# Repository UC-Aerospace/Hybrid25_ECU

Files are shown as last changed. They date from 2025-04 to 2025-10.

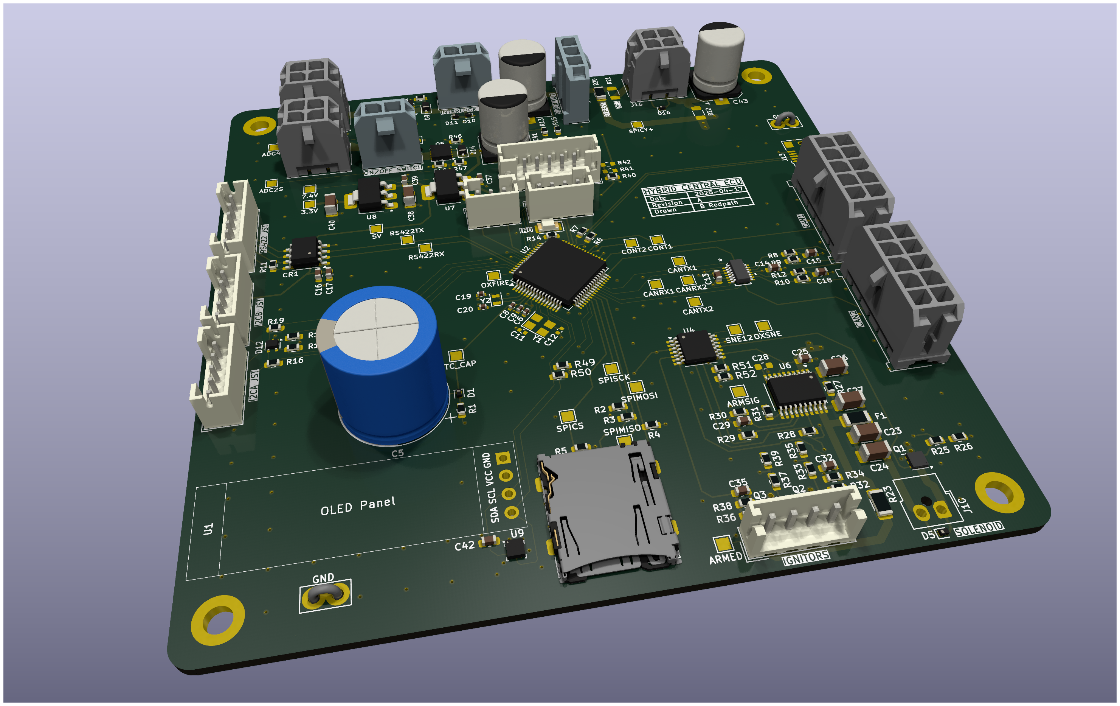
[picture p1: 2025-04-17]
Boards/Central_ECU/Render.png

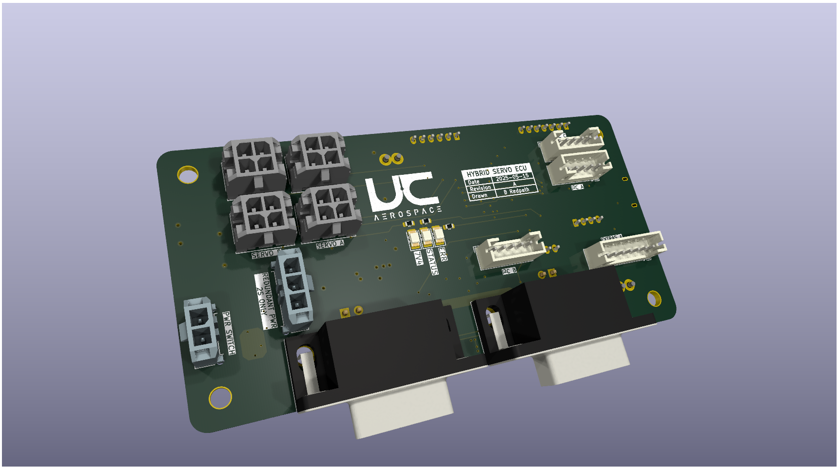
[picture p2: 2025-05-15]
Boards/Servo_Board/Render.png

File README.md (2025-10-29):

# Hybrid Engine Control Unit

This repo contains the hardware and firmware for the 2025 Hybrid Rocket Engine FYP test stand electronics.

The hardware consists of three seperate modules, the central ECU alongside a servo and ADC peripheral. Central to peripheral
communication uses CAN-FD and is designed to be modular, while communications to a remote interface unit is done over RS422.
For more information on the RIU it can be found [here](https://github.com/UC-Aerospace/Hybrid25_RIU).







Hotfire

## Hardware

First thing to note, make sure you read the [issue!](https://github.com/UC-Aerospace/Hybrid25_ECU/issues/1).

There are issues with these designs, keep them in mind for any future development.

### MCU

The hardware of all these boards has been based on the STM32G0 MCU as a platform. The selection process for this was pretty
much based on wanting to use a STM32 for experience and the G0 in particular has two CAN-FD modems and was quite affordable.
This was a mistake, although it ended up working out okay. The STM32G0 critically lacks a SDIO peripheral which is a much
faster and more robust way of interacting with a SD card than SPI, as well as lacking QSPI and only having one SPI bus,
which meant we couldn't implement external flash memory for logging to. Given the issues with SD cards on an actual launch
vechicle that has been experienced I would have the following reccomendations:

* If you make new hardware switch MCU. Still use a ST product but pivot to something with SDIO and QSPI. Look into the F4, F7, H4 and H7 lines.
* Then implement a system where logging happens to flash during a test/launch, and then copies to SD afterwards. This means transfer to a PC
is still easy, you still get the bulk storage of SD but don't rely on it during high vibration periods.
* Don't go for a dual core. The cost increase dosn't justify the advantage and the complexity is significant.
* On cost the total sum of all the electronics this year was large enough not to worry about penny pinching on the MCU you buy maybe 5 of. $8 to $15
is inconsequential and well worth it if it saves you time.

Otherwise though the G0 has served it's purpose well this year. Honestly I have no idea how close we are cutting it with processing time overhead,
the MCU is plenty fast but a lot of the external I/O is quite slow (comms, sensors, SD card). Buffering is the name of the game in cases like that,
and trying to pass as much off to hardware peripherals as possible. Future teams could investigate a switch back to FreeRTOS for more flexibility around
scheduling, this will save some headaches and add a bunch more.

### Layout

Theres a bit of an explaination for the actual hardware design ethos to get you started in the Central ECU board directory. Otherwise between the
boards the main thing to talk about is connectors, comms and power.

The connectors we used on the peripheral boards were a compromise. JST's should never really be used where they might see forces on the wires,
but they are also cheap and the budget was getting out of hand. We mitigated this when testing by externally strain relieving all wires connecting
to both peripheral boards. Also when thinking about connectors try to keep in mind that if something can be plugged into the wrong place, it will
be plugged into the wrong place. Try to keep connectors dissimilar where you can, at least where damage would occur if they went the other way.

Comms is over CAN-FD for the peripheral to central communication and RS422 for central to RIU communication. The descision for this came because
CAN sounded cool to play with and RS422 seemed like the easiest way to get comms upto a couple hundred meters away. Both of these descisions played
out pretty well, with software headaches for both but nothing too serious. The CAN just uses premade serial DB9 cables, as these are cheap and easy
to get hold of. DB9 connectors are really solid and lock well, plus are rated to about 3A per pin. For the link to the RIU we just used generic CAT5
cable, two of the pairs are used for RS422 with another used for the ESTOP signal lines. The plastic connectors on either end are a weakspot, it would
have been nice to use something like etherCON connectors but again, expensive.

Power is something that got changed up a few times. We use lipo batteries as the power source, the ECU has two and theres an extra for the servos. The
ECU has a 2S for general functions, which is also passed to the peripherals which they use. The servo board uses this for the 2 7.4V servos remaining also.
The other battery in the ECU, the 6S, is used for the solenoids and ignitors. This is the power that the ESTOP is inline with, cutting that will abort the
test due to the normally closed solenoid. Finally as we had to add 24V servos there is a seperate 6S battery dedicated to them during the test. This is suboptimal
as we have no insight into the level of it remotely during a test and the standby draw is quite high. If done again just plug this directly into the servo board
and move all servos to 24V. 

## Software

I have yet to find a way to make code sound interesting, and I don't think I'm going to manage it here either. I guess the main thing to point out is there is
a lot of code. Certainly more than I expected going into this, and it took significantly longer than I expected as well. Main word of advice with the software,
it is very easy to get yourself stuck in a trap of rushing rubbish code out.



There was an extended period this year when we were perpetually two weeks away from testing, and it probably shows in the code. In the end the hold up was with
another system, but the code was still blasted out dangerously fast regardless. Give yourself time in the beginning and temper the goals, its easy to add more
later but hard to strip them away with testing looming.

For some more specifics on the actual code I'll leave a quick README for the specifics under each boards code. Heres a quick rant from the EOY report though.

*All code and hardware design has been done in a single git repository. This was poor practice, in future break the code up into separate repositories, 
the only reason we could make a single repository work is because only one person was working on it. One of the main motivators for doing it this way was to enable
code reuse between the boards, for example the CAN module is common between all three and uses a symbolic linked folder. In future it would be worth investigating
using git submodules for the same thing. VS Code was used as the IDE for the ECU and peripherals, while STM32CubeIDE was used for the RIU. It is **strongly** recommended
that future teams do not use CubeIDE, while IDE’s are a preference eclipse is objectively terrible. The ST support for VS Code is good enough now that after installing
the extensions and CubeMX the development experience is much better.*

*The general layout for each board is given below:*



### Finite State Machine Diagrams

#### Central ECU



#### Servo Module



### ADC Module

The ADC module has no inherent state machine, it just reads sensors and sends these.

## Operational

### Safety

Safety has been one of the major concerns with this project. To try and mitigate some of those concerns the main solenoid
is normally closed, such that within 350 milliseconds of cutting the power it fully shuts. The ignitors, being potentially
explosive, were also identified as high risk. Therefore, both these items are on a seperate circuit. Two air gaps exist
in this loop, one E-Stop positioned inline and outside the test container, another at the RIU and connected through a relay
to limit current loss.





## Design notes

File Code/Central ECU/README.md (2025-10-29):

# Central ECU Code

If its your job in 2026 to work on this, good luck. Hopefully the base here is firm enough to build on but the code was
undeniably rushed. To get you started though:

### Layout

* All the user code is in the src/ or include/ folders. Everything else is the STM HAL primarily.
* The Core/Src/main.c file is the main code entry, this has been patched to call src/app.c after it sets everything up.
* The CMakeLists might have to be changed from time to time as well.
* A seriously major battle was fought over getting the SD card working.
Some of the FATFS files were modified in other places, the stuff I added is mainly in Middlewares/Third_Party/FatFs. I really hope no one else has to touch that.

The ECU_Mainboard.ioc can be opened in cubemx to configure most of the HAL options.

### Gotchas

1) The code is currently locked to a specific MCU. This is because I have a habbit of flashing the wrong code when working with
multiple tabs. It checks the UID of the MCU on entry to app.c and will abort if it dosn't match.
2) The code is set up with the intention to support more boards being added modularly but there would be at least a bit of work that has
to go into tweaking the communication protocols I suspect.
3) The SD card is slooooow. It can sometimes take upto 100ms, generally on a flush but it can be hard to predict. This is the reason a lot
of the buffers are so large.
4) The timebase has been changed from a systick interrupt to one of the hardware timers. This still drifts quite quickly (1ms+ every 10 seconds)
compared to the other boards. Switching all from the internal occilator to an external one by populating the part across all boards would improve this.

### Tasks

To see all the tasks head into the app.c file. The timings allocated to these could definitly be optimised but these were pretty much just what worked.
For a quick explaination of each:

#### task_poll_can_handlers()

CAN operates on a two level system. All frames have a priority set by the ID, priority 0 and 1 (error and heartbeat) and serviced in ISR context,
while priorities 2 and 3 (commands and data) are added to a buffer by the ISR and it returns. This buffer is then polled from the can_handler module,
which will decode it and take action based on the contents.

#### task_poll_rs422()

Similarly to how the CAN works the RS422 again uses a hardware and handler approach. This time as the RS422 is really just a UART peripheral the RX fifo
is serviced with DMA into a large circular buffer. This polling function then checks the circular buffer, and after checking the length byte if a full
frame exists in the buffer it will compute a CRC to validate it before decoding and actioning.

#### task_poll_battery()

Pretty simple this one, both batteries are connected to a ADC pin through a voltage divider so a reading is taken, converted to a voltage and then to a
percentage with a lookup table. This updates the OLED screen as well as sending the percentages over RS422.

#### test_servo_poll()

This is the debug USB interface and could be safely disabled for tests. This exposes a command line input over the USB serial port, both for moving the
servos and setting the internal real-time clock that is used in logs.

#### task_flush_sd_card()

When a write happens to the SD card it dosn't really occur. The SD card needs to be flushed to retain this after power loss, so we have to flush it every
now and again. Be warned, flushes can be slooow.

#### fsm_tick()

The main finite state machine, run the next iteration of it.

#### can_service_tx_queue()

Similarly to the revieve this will place messages from the software queue into the hardware tx queue. Upto 3 messages can be in the hardware buffer at once.

#### task_send_heartbeat()

Sends a heartbeat both over CAN broadcast and RS422.

#### spicy_send_status_update()

This is a really dumb name, but "spicy" refers to anything with the ignitors and solenoid which are on the "spicy" circuit. The RS422 frame for this was added
late, hence having its own task. It just sends a bunch of status information.

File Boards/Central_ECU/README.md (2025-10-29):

# Central ECU



The central ECU is pretty simple and carries out a couple of tasks. Firstly is comms which is easy to see with CAN on the left and RS422 on the right
of the schematic. The SD card occupies the top right, with pull up resistors on the main data lines. The top right has a display over I2C and a
pressure and temp sensor. On the status LED front the other boards had two controlled from GPIOs while the central ECU only has one. Two is much
better as you can have a status and error LED, don't discount just how useful a few LEDs are. And finally the interesting bit is probably the spicy stuff.



This is for the control of the single solenoid and two ignitor channels. The layout is very similar for both, except the ignitors have continuity detection
as well. First off theres a connector populated to allow for an external regulator if the voltage requirements of the solenoid changes. This occured as we
made this board before selecting a solenoid. A comparator then is used on the input so we know when the RIU and external ESTOP are released.

For the actual switching there is both a high and low side switch. The high side switch is common to both ignitors and solenoid, and comes in the form of a
EFuse. Theres some big advantages to doing it this way, for one it limits the current spike that occurs when switching the outputs, and also will protect the
circuit in the case of a shorted output. A GPIO toggles this, allowing for a hardware "Arm" controlled by software. A 2K resistor bypasses the highside switch,
this allows for continuity detection. Nominally no current will flow through this as the low side switches will be off, but even if one of the low side switches
is on the current is limited to 15mA, too low to ignite one of the ignitors or open the solenoid. This dual switching design also provides some reassurance in
the case of a FET failing as they usually fail shorted, allowing the test to be terminated by the ECU regardless of a single failure.



The connectors are another area that might be worth mentioning briefly. It is generally good practice to make sure that things physically can't be plugged in
wrong, because someone will definitly plug that 6S battery into your 2S circuit otherwise. You can see I have designed it such that the 2S and 6S input shares
the same sort of connector, but has the voltage on a different pin so if they get plugged in the wrong way around it dosn't matter. Doing this everywhere will
get impractical, for instance the on and arm switches are the same, but think about the critical places to do this and make sure you do. Either use a different
connector type or different number of pins to switch it up.

Final rant for this section, be careful with your linear voltage regulators. They will have a rated current but thats never really achievable due to thermals.
Make sure you actually do some thermal calculations and stitch the regulators through into the planes underneath with plenty of vias. And chaining the regulators
is another approach, I needed 5V but had very little 5V draw, so by inputting 5V to the 3.3V regulator you effectivly split the heat across both regulators.

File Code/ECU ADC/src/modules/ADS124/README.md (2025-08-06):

# ADS124S08 HAL Conversion for STM32

This document describes the conversion of the ADS124S08 Hardware Abstraction Layer (HAL) from TI Drivers to STM32 HAL.

## Overview

The ADS124S08 is a precision, 24-bit analog-to-digital converter (ADC) that communicates via SPI. The original code was designed for TI microcontrollers using TI Drivers. This conversion adapts it for STM32 microcontrollers using the STM32 HAL library.

## Changes Made

### 1. Header Files (`hal.h`)
- Replaced TI Drivers includes with STM32 HAL includes
- Updated pin definitions to match STM32G0 GPIO pins
- Converted function prototypes to use `SPI_HandleTypeDef*` instead of `SPI_Handle`

### 2. Implementation Files (`hal.c`)
- **Timing functions**: 
  - `delay_ms()`: Now uses `HAL_Delay()`
  - `delay_us()`: Implemented using cycle counting for microsecond precision
- **GPIO functions**: 
  - Converted to use `HAL_GPIO_WritePin()` and `HAL_GPIO_ReadPin()`
  - Updated interrupt handling to use STM32 EXTI callbacks
- **SPI functions**: 
  - Converted to use `HAL_SPI_TransmitReceive()`
  - Removed manual CS control (now handled by SPI peripheral)

### 3. ADS124 Driver (`ads124.c` and `ads124.h`)
- Updated all function signatures to use `SPI_HandleTypeDef*`
- Converted all SPI communication calls to use the new HAL functions

## Pin Mapping

The following STM32G0 pins are used for the ADS124S08 interface:

| ADS124S08 Signal | STM32G0 Pin | Description |
|---|---|---|
| nDRDY | PC5 (ADC_RDY) | Data Ready interrupt (falling edge) |
| nRESET | PB0 (ADC_RST) | Reset pin (active low) |
| START/SYNC | PC4 (SYNC) | Start/Sync pin |
| nCS | PA4 (SPI1_NSS)| Chip Select (auto-controlled by SPI) |
| SCLK | PA5 (SPI1_SCK)| SPI Clock |
| DIN | PA7 (SPI1_MOSI)| SPI Master Out Slave In |
| DOUT | PA6 (SPI1_MISO)| SPI Master In Slave Out |

## Usage Example

**IMPORTANT:** The `HAL_GPIO_EXTI_Callback` function MUST be implemented in your `main.c` file, not in the HAL library files. This is because it's a weak function in the STM32 HAL that needs to be overridden in your main application.

```c
#include "ads124_example.h"
#include "hal.h"  // For ads124_gpio_exti_callback

int main(void)
{
    // STM32 HAL initialization (generated by STM32CubeMX)
    HAL_Init();
    SystemClock_Config();
    MX_GPIO_Init();
    MX_SPI1_Init();
    
    // Initialize ADS124S08
    if (ads124_init() != HAL_OK) {
        Error_Handler();
    }
    
    // Start conversions
    ads124_start_conversion();
    
    // Main loop
    while (1) {
        int32_t adc_value;
        uint8_t status;
        
        if (ads124_read_conversion(&adc_value, &status) == HAL_OK) {
            // Process ADC value
            float voltage = (float)adc_value * 2.5f / 8388608.0f;
            // Do something with voltage...
        }
        
        HAL_Delay(100);
    }
}

// CRITICAL: This function MUST be in main.c to handle interrupts properly
void HAL_GPIO_EXTI_Callback(uint16_t GPIO_Pin)
{
    // Call the ADS124 interrupt handler
    ads124_gpio_exti_callback(GPIO_Pin);
    
    // Handle other GPIO interrupts if needed
    // if (GPIO_Pin == OTHER_PIN) { ... }
}
```

## STM32CubeMX Configuration

### SPI1 Configuration
- Mode: Full-Duplex Master
- Hardware NSS Signal: Output
- Clock Polarity: Low (CPOL = 0)
- Clock Phase: 2 Edge (CPHA = 1)
- Data Size: 8 Bits
- Baud Rate: 2 MHz (or as needed)

### GPIO Configuration
- PC5 (ADC_RDY): GPIO_EXTI5, Falling Edge, Pull-up
- PB0 (ADC_RST): GPIO_Output, High level
- PC4 (SYNC): GPIO_Output, Low level

### Interrupt Configuration
- Enable EXTI4_15_IRQn for the DRDY interrupt

## Important Notes

1. **SPI Mode**: The ADS124S08 requires SPI Mode 1 (CPOL=0, CPHA=1)
2. **Timing**: The microsecond delay function uses cycle counting and may need calibration for precise timing
3. **CRITICAL - Interrupts**: The `HAL_GPIO_EXTI_Callback` function MUST be implemented in your main.c file, not in the HAL library. This is because it's a weak function in STM32 HAL that needs to be overridden in the main application.
4. **CS Control**: Chip Select is handled automatically by the SPI peripheral in NSS Output mode
5. **Error Handling**: All SPI operations include error checking and call `Error_Handler()` on failure

### Interrupt Handler Implementation

The correct way to handle the ADS124S08 interrupt is:

1. **In your main.c file**, implement `HAL_GPIO_EXTI_Callback`:
```c
void HAL_GPIO_EXTI_Callback(uint16_t GPIO_Pin)
{
    ads124_gpio_exti_callback(GPIO_Pin);  // Call ADS124 handler
    // Handle other pins if needed
}
```

2. **Include the header**: `#include "hal.h"` in your main.c to access `ads124_gpio_exti_callback`

3. **Do NOT** define `HAL_GPIO_EXTI_Callback` in library files - it won't be called by the linker.

## Files Modified/Created

### Modified Files:
- `src/modules/ADS124/hal.h` - Updated for STM32 HAL
- `src/modules/ADS124/hal.c` - Converted to STM32 HAL implementation
- `src/modules/ADS124/ads124.h` - Updated function prototypes
- `src/modules/ADS124/ads124.c` - Updated function implementations

### New Files:
- `src/modules/ADS124/ads124_example.h` - Example usage header
- `src/modules/ADS124/ads124_example.c` - Example implementation

## Testing

To test the converted HAL:

1. Configure STM32CubeMX as described above
2. Include the ADS124 files in your project
3. Implement the example code in your main application
4. Verify SPI communication and ADC readings

## Future Improvements

1. Implement DWT-based microsecond timing for better precision
2. Add support for manual CS control if needed
3. Add comprehensive error handling and status reporting
4. Implement advanced ADS124S08 features (multiple channels, calibration, etc.)

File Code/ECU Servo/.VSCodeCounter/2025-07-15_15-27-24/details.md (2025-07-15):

# Details

Date : 2025-07-15 15:27:24

Directory /Users/bradr/Uni/FYP/Hybrid25_ECU/Code/ECU Servo

Total : 161 files,  93055 codes, 75724 comments, 24840 blanks, all 193619 lines

[Summary](results.md) / Details / [Diff Summary](diff.md) / [Diff Details](diff-details.md)

## Files
| filename | language | code | comment | blank | total |
| :--- | :--- | ---: | ---: | ---: | ---: |
| [CMakeCache.txt](/CMakeCache.txt) | CMake Cache | 329 | 0 | 73 | 402 |
| [CMakeFiles/4.0.1/CMakeASMCompiler.cmake](/CMakeFiles/4.0.1/CMakeASMCompiler.cmake) | CMake | 24 | 0 | 7 | 31 |
| [CMakeFiles/4.0.1/CMakeCCompiler.cmake](/CMakeFiles/4.0.1/CMakeCCompiler.cmake) | CMake | 66 | 0 | 18 | 84 |
| [CMakeFiles/4.0.1/CMakeCXXCompiler.cmake](/CMakeFiles/4.0.1/CMakeCXXCompiler.cmake) | CMake | 82 | 0 | 26 | 108 |
| [CMakeFiles/4.0.1/CMakeSystem.cmake](/CMakeFiles/4.0.1/CMakeSystem.cmake) | CMake | 10 | 0 | 6 | 16 |
| [CMakeFiles/4.0.1/CompilerIdC/CMakeCCompilerId.c](/CMakeFiles/4.0.1/CompilerIdC/CMakeCCompilerId.c) | C | 690 | 61 | 155 | 906 |
| [CMakeFiles/4.0.1/CompilerIdCXX/CMakeCXXCompilerId.cpp](/CMakeFiles/4.0.1/CompilerIdCXX/CMakeCXXCompilerId.cpp) | C++ | 708 | 62 | 151 | 921 |
| [CMakeFiles/CMakeConfigureLog.yaml](/CMakeFiles/CMakeConfigureLog.yaml) | YAML | 402 | 4 | 36 | 442 |
| [CMakeFiles/InstallScripts.json](/CMakeFiles/InstallScripts.json) | JSON | 8 | 0 | 1 | 9 |
| [CMakeFiles/VerifyGlobs.cmake](/CMakeFiles/VerifyGlobs.cmake) | CMake | 12 | 0 | 2 | 14 |
| [CMakeFiles/clean_additional.cmake](/CMakeFiles/clean_additional.cmake) | CMake | 7 | 0 | 2 | 9 |
| [CMakePresets.json](/CMakePresets.json) | JSON | 60 | 0 | 0 | 60 |
| [Core/Inc/main.h](/Core/Inc/main.h) | C++ | 56 | 39 | 21 | 116 |
| [Core/Inc/stm32g0xx_hal_conf.h](/Core/Inc/stm32g0xx_hal_conf.h) | C++ | 180 | 116 | 56 | 352 |
| [Core/Inc/stm32g0xx_it.h](/Core/Inc/stm32g0xx_it.h) | C++ | 15 | 34 | 15 | 64 |
| [Core/Src/main.c](/Core/Src/main.c) | C | 455 | 237 | 137 | 829 |
| [Core/Src/stm32g0xx_hal_msp.c](/Core/Src/stm32g0xx_hal_msp.c) | C | 279 | 351 | 159 | 789 |
| [Core/Src/stm32g0xx_it.c](/Core/Src/stm32g0xx_it.c) | C | 29 | 96 | 35 | 160 |
| [Core/Src/syscalls.c](/Core/Src/syscalls.c) | C | 123 | 25 | 29 | 177 |
| [Core/Src/sysmem.c](/Core/Src/sysmem.c) | C | 24 | 48 | 8 | 80 |
| [Core/Src/system_stm32g0xx.c](/Core/Src/system_stm32g0xx.c) | C | 74 | 194 | 35 | 303 |
| [Drivers/CMSIS/Device/ST/STM32G0xx/Include/stm32g0b1xx.h](/Drivers/CMSIS/Device/ST/STM32G0xx/Include/stm32g0b1xx.h) | C++ | 9,726 | 829 | 719 | 11,274 |
| [Drivers/CMSIS/Device/ST/STM32G0xx/Include/stm32g0xx.h](/Drivers/CMSIS/Device/ST/STM32G0xx/Include/stm32g0xx.h) | C++ | 119 | 89 | 37 | 245 |
| [Drivers/CMSIS/Device/ST/STM32G0xx/Include/system_stm32g0xx.h](/Drivers/CMSIS/Device/ST/STM32G0xx/Include/system_stm32g0xx.h) | C++ | 14 | 70 | 20 | 104 |
| [Drivers/CMSIS/Include/cmsis_armcc.h](/Drivers/CMSIS/Include/cmsis_armcc.h) | C++ | 401 | 355 | 139 | 895 |
| [Drivers/CMSIS/Include/cmsis_armclang.h](/Drivers/CMSIS/Include/cmsis_armclang.h) | C++ | 623 | 595 | 227 | 1,445 |
| [Drivers/CMSIS/Include/cmsis_armclang_ltm.h](/Drivers/CMSIS/Include/cmsis_armclang_ltm.h) | C++ | 948 | 595 | 349 | 1,892 |
| [Drivers/CMSIS/Include/cmsis_compiler.h](/Drivers/CMSIS/Include/cmsis_compiler.h) | C++ | 207 | 52 | 25 | 284 |
| [Drivers/CMSIS/Include/cmsis_gcc.h](/Drivers/CMSIS/Include/cmsis_gcc.h) | C++ | 1,170 | 620 | 379 | 2,169 |
| [Drivers/CMSIS/Include/cmsis_iccarm.h](/Drivers/CMSIS/Include/cmsis_iccarm.h) | C++ | 769 | 45 | 151 | 965 |
| [Drivers/CMSIS/Include/cmsis_version.h](/Drivers/CMSIS/Include/cmsis_version.h) | C++ | 13 | 23 | 4 | 40 |
| [Drivers/CMSIS/Include/core_armv81mml.h](/Drivers/CMSIS/Include/core_armv81mml.h) | C++ | 1,714 | 651 | 604 | 2,969 |
| [Drivers/CMSIS/Include/core_armv8mbl.h](/Drivers/CMSIS/Include/core_armv8mbl.h) | C++ | 1,033 | 526 | 363 | 1,922 |
| [Drivers/CMSIS/Include/core_armv8mml.h](/Drivers/CMSIS/Include/core_armv8mml.h) | C++ | 1,627 | 642 | 567 | 2,836 |
| [Drivers/CMSIS/Include/core_cm0.h](/Drivers/CMSIS/Include/core_cm0.h) | C++ | 444 | 327 | 182 | 953 |
| [Drivers/CMSIS/Include/core_cm0plus.h](/Drivers/CMSIS/Include/core_cm0plus.h) | C++ | 528 | 346 | 212 | 1,086 |
| [Drivers/CMSIS/Include/core_cm1.h](/Drivers/CMSIS/Include/core_cm1.h) | C++ | 454 | 338 | 188 | 980 |
| [Drivers/CMSIS/Include/core_cm23.h](/Drivers/CMSIS/Include/core_cm23.h) | C++ | 1,081 | 532 | 384 | 1,997 |
| [Drivers/CMSIS/Include/core_cm3.h](/Drivers/CMSIS/Include/core_cm3.h) | C++ | 1,051 | 468 | 419 | 1,938 |
| [Drivers/CMSIS/Include/core_cm33.h](/Drivers/CMSIS/Include/core_cm33.h) | C++ | 1,677 | 646 | 588 | 2,911 |
| [Drivers/CMSIS/Include/core_cm35p.h](/Drivers/CMSIS/Include/core_cm35p.h) | C++ | 1,677 | 646 | 588 | 2,911 |
| [Drivers/CMSIS/Include/core_cm4.h](/Drivers/CMSIS/Include/core_cm4.h) | C++ | 1,182 | 485 | 458 | 2,125 |
| [Drivers/CMSIS/Include/core_cm7.h](/Drivers/CMSIS/Include/core_cm7.h) | C++ | 1,571 | 576 | 579 | 2,726 |
| [Drivers/CMSIS/Include/core_sc000.h](/Drivers/CMSIS/Include/core_sc000.h) | C++ | 488 | 335 | 203 | 1,026 |
| [Drivers/CMSIS/Include/core_sc300.h](/Drivers/CMSIS/Include/core_sc300.h) | C++ | 1,034 | 467 | 412 | 1,913 |
| [Drivers/CMSIS/Include/mpu_armv7.h](/Drivers/CMSIS/Include/mpu_armv7.h) | C++ | 122 | 125 | 26 | 273 |
| [Drivers/CMSIS/Include/mpu_armv8.h](/Drivers/CMSIS/Include/mpu_armv8.h) | C++ | 168 | 135 | 44 | 347 |
| [Drivers/CMSIS/Include/tz_context.h](/Drivers/CMSIS/Include/tz_context.h) | C++ | 19 | 40 | 12 | 71 |
| [Drivers/STM32G0xx_HAL_Driver/Inc/Legacy/stm32_hal_legacy.h](/Drivers/STM32G0xx_HAL_Driver/Inc/Legacy/stm32_hal_legacy.h) | C++ | 2,895 | 616 | 409 | 3,920 |
| [Drivers/STM32G0xx_HAL_Driver/Inc/stm32g0xx_hal.h](/Drivers/STM32G0xx_HAL_Driver/Inc/stm32g0xx_hal.h) | C++ | 460 | 268 | 111 | 839 |
| [Drivers/STM32G0xx_HAL_Driver/Inc/stm32g0xx_hal_adc.h](/Drivers/STM32G0xx_HAL_Driver/Inc/stm32g0xx_hal_adc.h) | C++ | 521 | 1,248 | 175 | 1,944 |
| [Drivers/STM32G0xx_HAL_Driver/Inc/stm32g0xx_hal_adc_ex.h](/Drivers/STM32G0xx_HAL_Driver/Inc/stm32g0xx_hal_adc_ex.h) | C++ | 40 | 111 | 36 | 187 |
| [Drivers/STM32G0xx_HAL_Driver/Inc/stm32g0xx_hal_cortex.h](/Drivers/STM32G0xx_HAL_Driver/Inc/stm32g0xx_hal_cortex.h) | C++ | 164 | 171 | 53 | 388 |
| [Drivers/STM32G0xx_HAL_Driver/Inc/stm32g0xx_hal_def.h](/Drivers/STM32G0xx_HAL_Driver/Inc/stm32g0xx_hal_def.h) | C++ | 108 | 78 | 30 | 216 |
| [Drivers/STM32G0xx_HAL_Driver/Inc/stm32g0xx_hal_dma.h](/Drivers/STM32G0xx_HAL_Driver/Inc/stm32g0xx_hal_dma.h) | C++ | 428 | 274 | 102 | 804 |
| [Drivers/STM32G0xx_HAL_Driver/Inc/stm32g0xx_hal_dma_ex.h](/Drivers/STM32G0xx_HAL_Driver/Inc/stm32g0xx_hal_dma_ex.h) | C++ | 114 | 110 | 55 | 279 |
| [Drivers/STM32G0xx_HAL_Driver/Inc/stm32g0xx_hal_exti.h](/Drivers/STM32G0xx_HAL_Driver/Inc/stm32g0xx_hal_exti.h) | C++ | 201 | 142 | 45 | 388 |
| [Drivers/STM32G0xx_HAL_Driver/Inc/stm32g0xx_hal_fdcan.h](/Drivers/STM32G0xx_HAL_Driver/Inc/stm32g0xx_hal_fdcan.h) | C++ | 622 | 634 | 187 | 1,443 |
| [Drivers/STM32G0xx_HAL_Driver/Inc/stm32g0xx_hal_flash.h](/Drivers/STM32G0xx_HAL_Driver/Inc/stm32g0xx_hal_flash.h) | C++ | 446 | 490 | 98 | 1,034 |
| [Drivers/STM32G0xx_HAL_Driver/Inc/stm32g0xx_hal_flash_ex.h](/Drivers/STM32G0xx_HAL_Driver/Inc/stm32g0xx_hal_flash_ex.h) | C++ | 27 | 72 | 18 | 117 |
| [Drivers/STM32G0xx_HAL_Driver/Inc/stm32g0xx_hal_gpio.h](/Drivers/STM32G0xx_HAL_Driver/Inc/stm32g0xx_hal_gpio.h) | C++ | 124 | 188 | 51 | 363 |
| [Drivers/STM32G0xx_HAL_Driver/Inc/stm32g0xx_hal_gpio_ex.h](/Drivers/STM32G0xx_HAL_Driver/Inc/stm32g0xx_hal_gpio_ex.h) | C++ | 457 | 274 | 106 | 837 |
| [Drivers/STM32G0xx_HAL_Driver/Inc/stm32g0xx_hal_i2c.h](/Drivers/STM32G0xx_HAL_Driver/Inc/stm32g0xx_hal_i2c.h) | C++ | 326 | 396 | 117 | 839 |
| [Drivers/STM32G0xx_HAL_Driver/Inc/stm32g0xx_hal_i2c_ex.h](/Drivers/STM32G0xx_HAL_Driver/Inc/stm32g0xx_hal_i2c_ex.h) | C++ | 45 | 106 | 27 | 178 |
| [Drivers/STM32G0xx_HAL_Driver/Inc/stm32g0xx_hal_pcd.h](/Drivers/STM32G0xx_HAL_Driver/Inc/stm32g0xx_hal_pcd.h) | C++ | 244 | 283 | 103 | 630 |
| [Drivers/STM32G0xx_HAL_Driver/Inc/stm32g0xx_hal_pcd_ex.h](/Drivers/STM32G0xx_HAL_Driver/Inc/stm32g0xx_hal_pcd_ex.h) | C++ | 21 | 47 | 21 | 89 |
| [Drivers/STM32G0xx_HAL_Driver/Inc/stm32g0xx_hal_pwr.h](/Drivers/STM32G0xx_HAL_Driver/Inc/stm32g0xx_hal_pwr.h) | C++ | 100 | 186 | 40 | 326 |
| [Drivers/STM32G0xx_HAL_Driver/Inc/stm32g0xx_hal_pwr_ex.h](/Drivers/STM32G0xx_HAL_Driver/Inc/stm32g0xx_hal_pwr_ex.h) | C++ | 251 | 315 | 76 | 642 |
| [Drivers/STM32G0xx_HAL_Driver/Inc/stm32g0xx_hal_rcc.h](/Drivers/STM32G0xx_HAL_Driver/Inc/stm32g0xx_hal_rcc.h) | C++ | 1,882 | 997 | 291 | 3,170 |
| [Drivers/STM32G0xx_HAL_Driver/Inc/stm32g0xx_hal_rcc_ex.h](/Drivers/STM32G0xx_HAL_Driver/Inc/stm32g0xx_hal_rcc_ex.h) | C++ | 696 | 694 | 201 | 1,591 |
| [Drivers/STM32G0xx_HAL_Driver/Inc/stm32g0xx_hal_rtc.h](/Drivers/STM32G0xx_HAL_Driver/Inc/stm32g0xx_hal_rtc.h) | C++ | 369 | 457 | 164 | 990 |
| [Drivers/STM32G0xx_HAL_Driver/Inc/stm32g0xx_hal_rtc_ex.h](/Drivers/STM32G0xx_HAL_Driver/Inc/stm32g0xx_hal_rtc_ex.h) | C++ | 287 | 705 | 171 | 1,163 |
| [Drivers/STM32G0xx_HAL_Driver/Inc/stm32g0xx_hal_spi.h](/Drivers/STM32G0xx_HAL_Driver/Inc/stm32g0xx_hal_spi.h) | C++ | 298 | 441 | 113 | 852 |
| [Drivers/STM32G0xx_HAL_Driver/Inc/stm32g0xx_hal_spi_ex.h](/Drivers/STM32G0xx_HAL_Driver/Inc/stm32g0xx_hal_spi_ex.h) | C++ | 11 | 49 | 14 | 74 |
| [Drivers/STM32G0xx_HAL_Driver/Inc/stm32g0xx_hal_tim.h](/Drivers/STM32G0xx_HAL_Driver/Inc/stm32g0xx_hal_tim.h) | C++ | 1,136 | 1,064 | 270 | 2,470 |
| [Drivers/STM32G0xx_HAL_Driver/Inc/stm32g0xx_hal_tim_ex.h](/Drivers/STM32G0xx_HAL_Driver/Inc/stm32g0xx_hal_tim_ex.h) | C++ | 231 | 195 | 69 | 495 |
| [Drivers/STM32G0xx_HAL_Driver/Inc/stm32g0xx_hal_uart.h](/Drivers/STM32G0xx_HAL_Driver/Inc/stm32g0xx_hal_uart.h) | C++ | 545 | 997 | 204 | 1,746 |
| [Drivers/STM32G0xx_HAL_Driver/Inc/stm32g0xx_hal_uart_ex.h](/Drivers/STM32G0xx_HAL_Driver/Inc/stm32g0xx_hal_uart_ex.h) | C++ | 543 | 180 | 49 | 772 |
| [Drivers/STM32G0xx_HAL_Driver/Inc/stm32g0xx_ll_adc.h](/Drivers/STM32G0xx_HAL_Driver/Inc/stm32g0xx_ll_adc.h) | C++ | 1,208 | 3,979 | 310 | 5,497 |
| [Drivers/STM32G0xx_HAL_Driver/Inc/stm32g0xx_ll_bus.h](/Drivers/STM32G0xx_HAL_Driver/Inc/stm32g0xx_ll_bus.h) | C++ | 270 | 975 | 62 | 1,307 |
| [Drivers/STM32G0xx_HAL_Driver/Inc/stm32g0xx_ll_cortex.h](/Drivers/STM32G0xx_HAL_Driver/Inc/stm32g0xx_ll_cortex.h) | C++ | 177 | 349 | 60 | 586 |
| [Drivers/STM32G0xx_HAL_Driver/Inc/stm32g0xx_ll_crs.h](/Drivers/STM32G0xx_HAL_Driver/Inc/stm32g0xx_ll_crs.h) | C++ | 230 | 461 | 90 | 781 |
| [Drivers/STM32G0xx_HAL_Driver/Inc/stm32g0xx_ll_dma.h](/Drivers/STM32G0xx_HAL_Driver/Inc/stm32g0xx_ll_dma.h) | C++ | 712 | 1,408 | 151 | 2,271 |
| [Drivers/STM32G0xx_HAL_Driver/Inc/stm32g0xx_ll_dmamux.h](/Drivers/STM32G0xx_HAL_Driver/Inc/stm32g0xx_ll_dmamux.h) | C++ | 614 | 1,120 | 105 | 1,839 |
| [Drivers/STM32G0xx_HAL_Driver/Inc/stm32g0xx_ll_exti.h](/Drivers/STM32G0xx_HAL_Driver/Inc/stm32g0xx_ll_exti.h) | C++ | 350 | 1,109 | 99 | 1,558 |
| [Drivers/STM32G0xx_HAL_Driver/Inc/stm32g0xx_ll_gpio.h](/Drivers/STM32G0xx_HAL_Driver/Inc/stm32g0xx_ll_gpio.h) | C++ | 187 | 702 | 70 | 959 |
| [Drivers/STM32G0xx_HAL_Driver/Inc/stm32g0xx_ll_i2c.h](/Drivers/STM32G0xx_HAL_Driver/Inc/stm32g0xx_ll_i2c.h) | C++ | 678 | 1,404 | 198 | 2,280 |
| [Drivers/STM32G0xx_HAL_Driver/Inc/stm32g0xx_ll_lpuart.h](/Drivers/STM32G0xx_HAL_Driver/Inc/stm32g0xx_ll_lpuart.h) | C++ | 831 | 1,566 | 247 | 2,644 |
| [Drivers/STM32G0xx_HAL_Driver/Inc/stm32g0xx_ll_pwr.h](/Drivers/STM32G0xx_HAL_Driver/Inc/stm32g0xx_ll_pwr.h) | C++ | 483 | 918 | 128 | 1,529 |
| [Drivers/STM32G0xx_HAL_Driver/Inc/stm32g0xx_ll_rcc.h](/Drivers/STM32G0xx_HAL_Driver/Inc/stm32g0xx_ll_rcc.h) | C++ | 1,215 | 2,469 | 294 | 3,978 |
| [Drivers/STM32G0xx_HAL_Driver/Inc/stm32g0xx_ll_rtc.h](/Drivers/STM32G0xx_HAL_Driver/Inc/stm32g0xx_ll_rtc.h) | C++ | 1,231 | 2,603 | 382 | 4,216 |
| [Drivers/STM32G0xx_HAL_Driver/Inc/stm32g0xx_ll_spi.h](/Drivers/STM32G0xx_HAL_Driver/Inc/stm32g0xx_ll_spi.h) | C++ | 671 | 1,372 | 242 | 2,285 |
| [Drivers/STM32G0xx_HAL_Driver/Inc/stm32g0xx_ll_system.h](/Drivers/STM32G0xx_HAL_Driver/Inc/stm32g0xx_ll_system.h) | C++ | 823 | 1,092 | 171 | 2,086 |
| [Drivers/STM32G0xx_HAL_Driver/Inc/stm32g0xx_ll_tim.h](/Drivers/STM32G0xx_HAL_Driver/Inc/stm32g0xx_ll_tim.h) | C++ | 1,512 | 3,374 | 387 | 5,273 |
| [Drivers/STM32G0xx_HAL_Driver/Inc/stm32g0xx_ll_usart.h](/Drivers/STM32G0xx_HAL_Driver/Inc/stm32g0xx_ll_usart.h) | C++ | 1,274 | 2,764 | 362 | 4,400 |
| [Drivers/STM32G0xx_HAL_Driver/Inc/stm32g0xx_ll_usb.h](/Drivers/STM32G0xx_HAL_Driver/Inc/stm32g0xx_ll_usb.h) | C++ | 473 | 285 | 157 | 915 |
| [Drivers/STM32G0xx_HAL_Driver/Inc/stm32g0xx_ll_utils.h](/Drivers/STM32G0xx_HAL_Driver/Inc/stm32g0xx_ll_utils.h) | C++ | 93 | 207 | 44 | 344 |
| [Drivers/STM32G0xx_HAL_Driver/Src/stm32g0xx_hal.c](/Drivers/STM32G0xx_HAL_Driver/Src/stm32g0xx_hal.c) | C | 248 | 429 | 84 | 761 |
| [Drivers/STM32G0xx_HAL_Driver/Src/stm32g0xx_hal_adc.c](/Drivers/STM32G0xx_HAL_Driver/Src/stm32g0xx_hal_adc.c) | C | 1,271 | 1,348 | 369 | 2,988 |
| [Drivers/STM32G0xx_HAL_Driver/Src/stm32g0xx_hal_adc_ex.c](/Drivers/STM32G0xx_HAL_Driver/Src/stm32g0xx_hal_adc_ex.c) | C | 144 | 200 | 66 | 410 |
| [Drivers/STM32G0xx_HAL_Driver/Src/stm32g0xx_hal_cortex.c](/Drivers/STM32G0xx_HAL_Driver/Src/stm32g0xx_hal_cortex.c) | C | 115 | 281 | 48 | 444 |
| [Drivers/STM32G0xx_HAL_Driver/Src/stm32g0xx_hal_dma.c](/Drivers/STM32G0xx_HAL_Driver/Src/stm32g0xx_hal_dma.c) | C | 524 | 479 | 191 | 1,194 |
| [Drivers/STM32G0xx_HAL_Driver/Src/stm32g0xx_hal_dma_ex.c](/Drivers/STM32G0xx_HAL_Driver/Src/stm32g0xx_hal_dma_ex.c) | C | 110 | 162 | 49 | 321 |
| [Drivers/STM32G0xx_HAL_Driver/Src/stm32g0xx_hal_exti.c](/Drivers/STM32G0xx_HAL_Driver/Src/stm32g0xx_hal_exti.c) | C | 296 | 270 | 105 | 671 |
| [Drivers/STM32G0xx_HAL_Driver/Src/stm32g0xx_hal_fdcan.c](/Drivers/STM32G0xx_HAL_Driver/Src/stm32g0xx_hal_fdcan.c) | C | 1,690 | 1,393 | 458 | 3,541 |
| [Drivers/STM32G0xx_HAL_Driver/Src/stm32g0xx_hal_flash.c](/Drivers/STM32G0xx_HAL_Driver/Src/stm32g0xx_hal_flash.c) | C | 260 | 367 | 104 | 731 |
| [Drivers/STM32G0xx_HAL_Driver/Src/stm32g0xx_hal_flash_ex.c](/Drivers/STM32G0xx_HAL_Driver/Src/stm32g0xx_hal_flash_ex.c) | C | 582 | 577 | 151 | 1,310 |
| [Drivers/STM32G0xx_HAL_Driver/Src/stm32g0xx_hal_gpio.c](/Drivers/STM32G0xx_HAL_Driver/Src/stm32g0xx_hal_gpio.c) | C | 195 | 290 | 66 | 551 |
| [Drivers/STM32G0xx_HAL_Driver/Src/stm32g0xx_hal_i2c.c](/Drivers/STM32G0xx_HAL_Driver/Src/stm32g0xx_hal_i2c.c) | C | 3,983 | 2,438 | 1,058 | 7,479 |
| [Drivers/STM32G0xx_HAL_Driver/Src/stm32g0xx_hal_i2c_ex.c](/Drivers/STM32G0xx_HAL_Driver/Src/stm32g0xx_hal_i2c_ex.c) | C | 98 | 208 | 59 | 365 |
| [Drivers/STM32G0xx_HAL_Driver/Src/stm32g0xx_hal_pcd.c](/Drivers/STM32G0xx_HAL_Driver/Src/stm32g0xx_hal_pcd.c) | C | 1,204 | 699 | 347 | 2,250 |
| [Drivers/STM32G0xx_HAL_Driver/Src/stm32g0xx_hal_pcd_ex.c](/Drivers/STM32G0xx_HAL_Driver/Src/stm32g0xx_hal_pcd_ex.c) | C | 142 | 146 | 46 | 334 |
| [Drivers/STM32G0xx_HAL_Driver/Src/stm32g0xx_hal_pwr.c](/Drivers/STM32G0xx_HAL_Driver/Src/stm32g0xx_hal_pwr.c) | C | 110 | 384 | 49 | 543 |
| [Drivers/STM32G0xx_HAL_Driver/Src/stm32g0xx_hal_pwr_ex.c](/Drivers/STM32G0xx_HAL_Driver/Src/stm32g0xx_hal_pwr_ex.c) | C | 426 | 450 | 141 | 1,017 |
| [Drivers/STM32G0xx_HAL_Driver/Src/stm32g0xx_hal_rcc.c](/Drivers/STM32G0xx_HAL_Driver/Src/stm32g0xx_hal_rcc.c) | C | 702 | 614 | 157 | 1,473 |
| [Drivers/STM32G0xx_HAL_Driver/Src/stm32g0xx_hal_rcc_ex.c](/Drivers/STM32G0xx_HAL_Driver/Src/stm32g0xx_hal_rcc_ex.c) | C | 973 | 527 | 179 | 1,679 |
| [Drivers/STM32G0xx_HAL_Driver/Src/stm32g0xx_hal_rtc.c](/Drivers/STM32G0xx_HAL_Driver/Src/stm32g0xx_hal_rtc.c) | C | 925 | 730 | 268 | 1,923 |
| [Drivers/STM32G0xx_HAL_Driver/Src/stm32g0xx_hal_rtc_ex.c](/Drivers/STM32G0xx_HAL_Driver/Src/stm32g0xx_hal_rtc_ex.c) | C | 740 | 857 | 386 | 1,983 |
| [Drivers/STM32G0xx_HAL_Driver/Src/stm32g0xx_hal_spi.c](/Drivers/STM32G0xx_HAL_Driver/Src/stm32g0xx_hal_spi.c) | C | 2,568 | 1,342 | 520 | 4,430 |
| [Drivers/STM32G0xx_HAL_Driver/Src/stm32g0xx_hal_spi_ex.c](/Drivers/STM32G0xx_HAL_Driver/Src/stm32g0xx_hal_spi_ex.c) | C | 20 | 79 | 14 | 113 |
| [Drivers/STM32G0xx_HAL_Driver/Src/stm32g0xx_hal_tim.c](/Drivers/STM32G0xx_HAL_Driver/Src/stm32g0xx_hal_tim.c) | C | 4,103 | 2,738 | 1,091 | 7,932 |
| [Drivers/STM32G0xx_HAL_Driver/Src/stm32g0xx_hal_tim_ex.c](/Drivers/STM32G0xx_HAL_Driver/Src/stm32g0xx_hal_tim_ex.c) | C | 1,304 | 1,163 | 391 | 2,858 |
| [Drivers/STM32G0xx_HAL_Driver/Src/stm32g0xx_hal_uart.c](/Drivers/STM32G0xx_HAL_Driver/Src/stm32g0xx_hal_uart.c) | C | 2,423 | 1,696 | 644 | 4,763 |
| [Drivers/STM32G0xx_HAL_Driver/Src/stm32g0xx_hal_uart_ex.c](/Drivers/STM32G0xx_HAL_Driver/Src/stm32g0xx_hal_uart_ex.c) | C | 373 | 561 | 157 | 1,091 |
| [Drivers/STM32G0xx_HAL_Driver/Src/stm32g0xx_ll_adc.c](/Drivers/STM32G0xx_HAL_Driver/Src/stm32g0xx_ll_adc.c) | C | 375 | 319 | 85 | 779 |
| [Drivers/STM32G0xx_HAL_Driver/Src/stm32g0xx_ll_rcc.c](/Drivers/STM32G0xx_HAL_Driver/Src/stm32g0xx_ll_rcc.c) | C | 869 | 334 | 178 | 1,381 |
| [Drivers/STM32G0xx_HAL_Driver/Src/stm32g0xx_ll_usb.c](/Drivers/STM32G0xx_HAL_Driver/Src/stm32g0xx_ll_usb.c) | C | 812 | 447 | 193 | 1,452 |
| [Middlewares/ST/STM32_USB_Device_Library/Class/CDC/Inc/usbd_cdc.h](/Middlewares/ST/STM32_USB_Device_Library/Class/CDC/Inc/usbd_cdc.h) | C++ | 85 | 66 | 34 | 185 |
| [Middlewares/ST/STM32_USB_Device_Library/Class/CDC/Src/usbd_cdc.c](/Middlewares/ST/STM32_USB_Device_Library/Class/CDC/Src/usbd_cdc.c) | C | 508 | 249 | 138 | 895 |
| [Middlewares/ST/STM32_USB_Device_Library/Core/Inc/usbd_core.h](/Middlewares/ST/STM32_USB_Device_Library/Core/Inc/usbd_core.h) | C++ | 68 | 63 | 42 | 173 |
| [Middlewares/ST/STM32_USB_Device_Library/Core/Inc/usbd_ctlreq.h](/Middlewares/ST/STM32_USB_Device_Library/Core/Inc/usbd_ctlreq.h) | C++ | 16 | 62 | 24 | 102 |
| [Middlewares/ST/STM32_USB_Device_Library/Core/Inc/usbd_def.h](/Middlewares/ST/STM32_USB_Device_Library/Core/Inc/usbd_def.h) | C++ | 357 | 76 | 82 | 515 |
| [Middlewares/ST/STM32_USB_Device_Library/Core/Inc/usbd_ioreq.h](/Middlewares/ST/STM32_USB_Device_Library/Core/Inc/usbd_ioreq.h) | C++ | 22 | 62 | 30 | 114 |
| [Middlewares/ST/STM32_USB_Device_Library/Core/Src/usbd_core.c](/Middlewares/ST/STM32_USB_Device_Library/Core/Src/usbd_core.c) | C | 715 | 336 | 171 | 1,222 |
| [Middlewares/ST/STM32_USB_Device_Library/Core/Src/usbd_ctlreq.c](/Middlewares/ST/STM32_USB_Device_Library/Core/Src/usbd_ctlreq.c) | C | 734 | 175 | 143 | 1,052 |
| [Middlewares/ST/STM32_USB_Device_Library/Core/Src/usbd_ioreq.c](/Middlewares/ST/STM32_USB_Device_Library/Core/Src/usbd_ioreq.c) | C | 55 | 127 | 43 | 225 |
| [STM32G0B1XX_FLASH.ld](/STM32G0B1XX_FLASH.ld) | LinkerScript | 117 | 64 | 27 | 208 |
| [USB_Device/App/usb_device.c](/USB_Device/App/usb_device.c) | C | 23 | 54 | 21 | 98 |
| [USB_Device/App/usb_device.h](/USB_Device/App/usb_device.h) | C++ | 13 | 67 | 24 | 104 |
| [USB_Device/App/usbd_cdc_if.c](/USB_Device/App/usbd_cdc_if.c) | C | 79 | 185 | 66 | 330 |
| [USB_Device/App/usbd_cdc_if.h](/USB_Device/App/usbd_cdc_if.h) | C++ | 14 | 84 | 35 | 133 |
| [USB_Device/App/usbd_desc.c](/USB_Device/App/usbd_desc.c) | C | 167 | 166 | 64 | 397 |
| [USB_Device/App/usbd_desc.h](/USB_Device/App/usbd_desc.h) | C++ | 15 | 90 | 39 | 144 |
| [USB_Device/Target/usbd_conf.c](/USB_Device/Target/usbd_conf.c) | C | 356 | 315 | 132 | 803 |
| [USB_Device/Target/usbd_conf.h](/USB_Device/Target/usbd_conf.h) | C++ | 48 | 91 | 36 | 175 |
| [X-CUBE-MEMS1/Target/custom_mems_conf.h](/X-CUBE-MEMS1/Target/custom_mems_conf.h) | C++ | 17 | 21 | 10 | 48 |
| [X-CUBE-MEMS1/Target/custom_mems_conf_app.h](/X-CUBE-MEMS1/Target/custom_mems_conf_app.h) | C++ | 966 | 20 | 65 | 1,051 |
| [X-CUBE-MEMS1/Target/sensor_unicleo_id.h](/X-CUBE-MEMS1/Target/sensor_unicleo_id.h) | C++ | 78 | 23 | 10 | 111 |
| [cmake/gcc-arm-none-eabi.cmake](/cmake/gcc-arm-none-eabi.cmake) | CMake | 34 | 0 | 11 | 45 |
| [cmake/stm32cubemx/cmake_install.cmake](/cmake/stm32cubemx/cmake_install.cmake) | CMake | 39 | 0 | 7 | 46 |
| [cmake_install.cmake](/cmake_install.cmake) | CMake | 58 | 0 | 9 | 67 |
| [compile_commands.json](/compile_commands.json) | JSON | 290 | 0 | 0 | 290 |
| [include/config.h](/include/config.h) | C++ | 56 | 2 | 8 | 66 |
| [include/peripherals.h](/include/peripherals.h) | C++ | 16 | 1 | 4 | 21 |
| [src/app.c](/src/app.c) | C | 20 | 2 | 5 | 27 |
| [src/app.h](/src/app.h) | C++ | 8 | 3 | 4 | 15 |
| [src/modules/debug_io/debug_io.c](/src/modules/debug_io/debug_io.c) | C | 61 | 12 | 14 | 87 |
| [src/modules/debug_io/debug_io.h](/src/modules/debug_io/debug_io.h) | C++ | 6 | 2 | 3 | 11 |
| [src/modules/rtc_helper/rtc_helper.c](/src/modules/rtc_helper/rtc_helper.c) | C | 63 | 8 | 9 | 80 |
| [src/modules/rtc_helper/rtc_helper.h](/src/modules/rtc_helper/rtc_helper.h) | C++ | 9 | 0 | 3 | 12 |
| [startup_stm32g0b1xx.s](/startup_stm32g0b1xx.s) | Assembly | 240 | 0 | 57 | 297 |

[Summary](results.md) / Details / [Diff Summary](diff.md) / [Diff Details](diff-details.md)

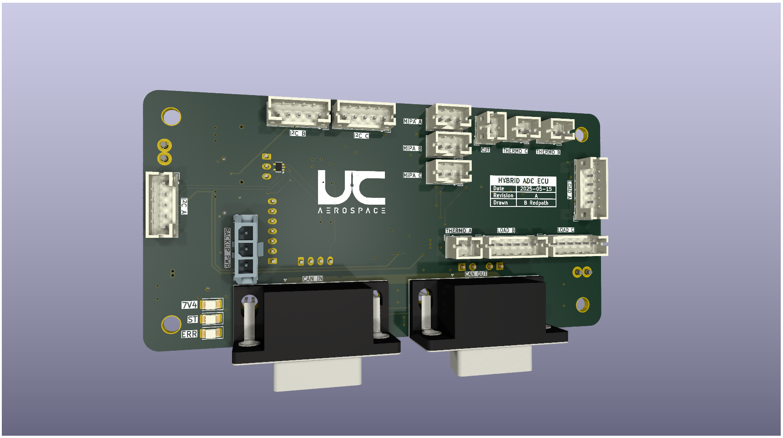
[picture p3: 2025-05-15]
Boards/ADC_Board/Render.png

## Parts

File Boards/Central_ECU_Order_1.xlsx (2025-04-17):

Reference | Qty | Value | Footprint | MPN | ORDER FROM
C1,C4,C37,C39 | 4 | 10u | Capacitor_SMD:C_0603_1608Metric |  | LCSC
C2,C3,C13,C14,C15,C17,C18,C25,C29,C32,C35,C42 | 12 | 100n | Capacitor_SMD:C_0603_1608Metric |  | LCSC
C5 | 1 | 100m | Capacitor_THT:CP_Radial_D14.0mm_P5.00mm | RSCBN1045R5G07014T | DIGIKEY
C6,C8,C9 | 3 | 100n | Capacitor_SMD:C_0402_1005Metric |  | LCSC
C7,C10,C16 | 3 | 4u7 | Capacitor_SMD:C_0603_1608Metric |  | LCSC
C11,C12 | 2 | ? | Capacitor_SMD:C_0402_1005Metric |  | N/A
C19,C20 | 2 | 12p | Capacitor_SMD:C_0402_1005Metric |  | LCSC
C23, C24, C26, C27, C30, C31, C33, C34 | 8 | 10u | Capacitor_SMD:C_1206_3216Metric |  | LCSC
C38,C40 | 2 | 22u | Capacitor_SMD:C_1206_3216Metric |  | LCSC
C28 | 1 | ? | Capacitor_SMD:C_0603_1608Metric |  | N/A
C36,C41,C43 | 3 | 100u | Capacitor_SMD:CP_Elec_8x10.5 | A768KS107M1HLAE030 | DIGIKEY
CR1 | 1 | ST490ABDR | Package_SO:SO-8_3.9x4.9mm_P1.27mm | ST490ABDR | DIGIKEY
D1,D5,D11 | 3 | D_Schottky | Diode_SMD:D_SOD-882 | CTS05S40,L3F | DIGIKEY
D2 | 1 | LED_R | LED_SMD:LED_1206_3216Metric | LTST-C150KRKT | DIGIKEY
D3 | 1 | LED_G | LED_SMD:LED_1206_3216Metric | LTST-C150KGKT | DIGIKEY
D4 | 1 | LED_B | LED_SMD:LED_1206_3216Metric | LTST-C150TBKT | DIGIKEY
D7,D15 | 2 | TVS 30V | Diode_SMD:D_SOD-882 | PESD1CANFD30L-QYL | DIGIKEY
D8,D10,D16 | 3 | 30V 34VC | Diode_SMD:D_SOD-882 | PESD1CANFD30L-QYL | DIGIKEY
D9,D14 | 2 | 18V | Diode_SMD:D_SOD-323F | MM3Z18VB | DIGIKEY
D12 | 1 | PESD3V3L4UW | Package_TO_SOT_SMD:SOT-665 | PESD3V3L4UW,115 | DIGIKEY
D13 | 1 | 9V 15.4VC | Diode_SMD:D_SOD-123F | SMF9.0CA | DIGIKEY
F1 | 1 | 2A | Fuse:Fuse_1206_3216Metric |  | LCSC
F2 | 1 | 4A | Fuse:Fuse_1206_3216Metric |  | LCSC
F3 | 1 | 5A | Fuse:Fuse_1206_3216Metric |  | LCSC
J1 | 1 | Micro_SD_Card | Connector_Card:microSD_HC_Molex_47219-2001 | 472192001 | DIGIKEY
J2 | 1 | Extras JST | Connector_JST:JST_PH_B7B-PH-K_1x07_P2.00mm_Vertical | B7B-PH-K-S | LCSC
J3,J6,J16 | 3 | MICROFIT | Connector_Molex:Molex_Micro-Fit_3.0_43045-0412_2x02_P3.00mm_Vertical | 430450412 | LCSC
J4 | 1 | Siren MICROFIT | Connector_Molex:Molex_Micro-Fit_3.0_43650-0315_1x03_P3.00mm_Vertical | 436500315 | LCSC
J5 | 1 | I2CB JST | Connector_JST:JST_PH_B5B-PH-K_1x05_P2.00mm_Vertical | B6B-PH-K-S | LCSC
J7 | 1 | I2CA JST | Connector_JST:JST_PH_B5B-PH-K_1x05_P2.00mm_Vertical | B5B-PH-K-S | LCSC
J8 | 1 | Ignitor JST EH | Connector_JST:JST_EH_B4B-EH-A_1x04_P2.50mm_Vertical | B4B-PH-K-S | LCSC
J9 | 1 | DB9 MICROFIT | Connector_Molex:Molex_Micro-Fit_3.0_43045-1012_2x05_P3.00mm_Vertical | 430451027 | DIGIKEY
J10 | 1 | Solenoid NANOFIT | Connector_Molex:Molex_Nano-Fit_105309-xx02_1x02_P2.50mm_Vertical | 1053091102 | DIGIKEY
J11 | 1 | DB9 Microfit | Connector_Molex:Molex_Micro-Fit_3.0_43045-1012_2x05_P3.00mm_Vertical | 430451027 | DIGIKEY
J12 | 1 | RS422 JST | Connector_JST:JST_PH_B6B-PH-K_1x06_P2.00mm_Vertical | B6B-PH-K-S | LCSC
J13 | 1 | USB_B_Micro | Connector_USB:USB_Micro-B_Amphenol_10118193-0001LF_Horizontal | 10118193-0001LF | DIGIKEY
J14 | 1 | SWD JST PH | Connector_JST:JST_PH_B4B-PH-K_1x04_P2.00mm_Vertical | B4B-PH-K-S | LCSC
J15 | 1 | UART JST | Connector_JST:JST_PH_B3B-PH-K_1x03_P2.00mm_Vertical | B3B-PH-K-S | LCSC
Q1,Q2,Q3 | 3 | DMT12H060LFDF | Package_DFN_QFN:Diodes_UDFN2020-6_Type-F | DMT12H060LFDF-7 | DIGIKEY
Q4,Q5 | 2 | DMP6023LFG | Package_SON:Diodes_PowerDI3333-8 | DMP6023LFG-7 | DIGIKEY
R1 | 1 | 33R | Resistor_SMD:R_0603_1608Metric |  | LCSC
R2,R3,R4,R5,R32,R34,R36,R38 | 8 | 20K | Resistor_SMD:R_0603_1608Metric |  | LCSC
R6,R7 | 2 | 27R | Resistor_SMD:R_0603_1608Metric |  | LCSC
R8,R9,R10,R12 | 4 | 60.4R | Resistor_SMD:R_0603_1608Metric |  | LCSC
R11 | 1 | 100R | Resistor_SMD:R_0603_1608Metric |  | LCSC
R13 | 1 | 330R | Resistor_SMD:R_0603_1608Metric |  | LCSC
R14 | 1 | 220R | Resistor_SMD:R_0603_1608Metric |  | LCSC
R15 | 1 | 1K | Resistor_SMD:R_0603_1608Metric |  | LCSC
R16,R17,R18,R19,R28,R49,R50,R51,R52 | 9 | 10K | Resistor_SMD:R_0603_1608Metric |  | LCSC
R20,R23 | 2 | 0R | Resistor_SMD:R_1206_3216Metric |  | LCSC
R21,R22 | 2 | 0R | Resistor_SMD:R_1206_3216Metric |  | LCSC
R25,R33,R37 | 3 | 549 | Resistor_SMD:R_0603_1608Metric |  | LCSC
R26,R35,R39 | 3 | 3.3K | Resistor_SMD:R_0603_1608Metric |  | LCSC
R27 | 1 | 2K | Resistor_SMD:R_0603_1608Metric |  | LCSC
R29 | 1 | 35K7 | Resistor_SMD:R_0603_1608Metric |  | LCSC
R30 | 1 | 10k | Resistor_SMD:R_0603_1608Metric |  | LCSC
R31 | 1 | 6K2 | Resistor_SMD:R_0603_1608Metric |  | LCSC
R40 | 1 | 0R | Resistor_SMD:R_0603_1608Metric |  | LCSC
R41,R42 | 2 | 0R | Resistor_SMD:R_0603_1608Metric |  | LCSC
R43,R46 | 2 | 100K | Resistor_SMD:R_0603_1608Metric |  | LCSC
R44 | 1 | 10K2 | Resistor_SMD:R_0603_1608Metric |  | LCSC
R45 | 1 | 2K49 | Resistor_SMD:R_0603_1608Metric |  | LCSC
R47 | 1 | 14K3 | Resistor_SMD:R_0603_1608Metric |  | LCSC
R48 | 1 | 9K53 | Resistor_SMD:R_0603_1608Metric |  | LCSC
SW1 | 1 | Arm Switch | Connector_Molex:Molex_Micro-Fit_3.0_43650-0215_1x02_P3.00mm_Vertical | 436500228 | DIGIKEY
SW2 | 1 | On Switch | Connector_Molex:Molex_Micro-Fit_3.0_43650-0215_1x02_P3.00mm_Vertical | 436500228 | DIGIKEY
TP1 | 1 | RTC_CAP | TestPoint:TestPoint_Pad_1.5x1.5mm |  | N/A
TP2 | 1 | ADC4S | TestPoint:TestPoint_Pad_1.5x1.5mm |  | N/A
TP3 | 1 | ADC2S | TestPoint:TestPoint_Pad_1.5x1.5mm |  | N/A
TP4 | 1 | SPISCK | TestPoint:TestPoint_Pad_1.5x1.5mm |  | N/A
TP5 | 1 | SPIMISO | TestPoint:TestPoint_Pad_1.5x1.5mm |  | N/A
TP6 | 1 | SPIMOSI | TestPoint:TestPoint_Pad_1.5x1.5mm |  | N/A
TP7 | 1 | SPICS | TestPoint:TestPoint_Pad_1.5x1.5mm |  | N/A
TP8 | 1 | CANTX1 | TestPoint:TestPoint_Pad_1.5x1.5mm |  | N/A
TP9 | 1 | CANRX1 | TestPoint:TestPoint_Pad_1.5x1.5mm |  | N/A
TP10 | 1 | CANTX2 | TestPoint:TestPoint_Pad_1.5x1.5mm |  | N/A
TP11 | 1 | CANRX2 | TestPoint:TestPoint_Pad_1.5x1.5mm |  | N/A
TP12 | 1 | CONT2 | TestPoint:TestPoint_Pad_1.5x1.5mm |  | N/A
TP13 | 1 | CONT1 | TestPoint:TestPoint_Pad_1.5x1.5mm |  | N/A
TP14 | 1 | RS422TX | TestPoint:TestPoint_Pad_1.5x1.5mm |  | N/A
TP15 | 1 | OXSNE | TestPoint:TestPoint_Pad_1.5x1.5mm |  | N/A
TP16 | 1 | RS422RX | TestPoint:TestPoint_Pad_1.5x1.5mm |  | N/A
TP17 | 1 | SNE12 | TestPoint:TestPoint_Pad_1.5x1.5mm |  | N/A
TP18 | 1 | OXFIRE | TestPoint:TestPoint_Pad_1.5x1.5mm |  | N/A
TP19 | 1 | EMCH2 | TestPoint:TestPoint_Pad_1.5x1.5mm |  | N/A
TP20 | 1 | EMCH1 | TestPoint:TestPoint_Pad_1.5x1.5mm |  | N/A
TP21 | 1 | ARMSIG | TestPoint:TestPoint_Pad_1.5x1.5mm |  | N/A
TP22 | 1 | IMON | TestPoint:TestPoint_Pad_1.5x1.5mm |  | N/A
TP23 | 1 | PGOOD | TestPoint:TestPoint_Pad_1.5x1.5mm |  | N/A
TP24 | 1 | 7.4V | TestPoint:TestPoint_Pad_1.5x1.5mm |  | N/A
TP25 | 1 | 5V | TestPoint:TestPoint_Pad_1.5x1.5mm |  | N/A
TP26 | 1 | 3.3V | TestPoint:TestPoint_Pad_1.5x1.5mm |  | N/A
TP27,TP28 | 2 | GND | TestPoint:TestPoint_Bridge_Pitch2.54mm_Drill1.3mm |  | N/A
TP29 | 1 | SPICY+ | TestPoint:TestPoint_Pad_1.5x1.5mm |  | N/A
TP30 | 1 | ARMED | TestPoint:TestPoint_Pad_1.5x1.5mm |  | N/A
TP31 | 1 | ADC2 | TestPoint:TestPoint_Pad_1.5x1.5mm |  | N/A
TP32 | 1 | ADC3 | TestPoint:TestPoint_Pad_1.5x1.5mm |  | N/A
U1 | 1 | SSD1306 | Custom:SSD1306-0.91-OLED-4pin-128x32 | N/A | N/A
U2 | 1 | STM32G0B1RCTx | Package_QFP:LQFP-64_10x10mm_P0.5mm | STM32G0B1RCT6 | DIGIKEY
U3 | 1 | TCAN1046 | Custom:SOT23_DYY_TEX | TCAN1046AVDYYRQ1 | DIGIKEY
U4 | 1 | LM339B | Package_SO:TSSOP-14_4.4x5mm_P0.65mm | LM339BIPWR | DIGIKEY
U6 | 1 | TPS16630PWPR | Package_SO:HTSSOP-20-1EP_4.4x6.5mm_P0.65mm_EP3.4x6.5mm_Mask2.96x2.96mm_ThermalVias | TPS16630PWPR | DIGIKEY
U7 | 1 | AZ1117C-5.0 | Package_TO_SOT_SMD:SOT-223-3_TabPin2 | AZ1117CH-5.0TRG1 | DIGIKEY
U8 | 1 | AZ1117C-3.3 | Package_TO_SOT_SMD:SOT-223-3_TabPin2 | AZ1117CH-3.3TRG1 | DIGIKEY
U9 | 1 | LPS22HH | Package_LGA:ST_HLGA-10_2x2mm_P0.5mm_LayoutBorder3x2y | LPS22HHTR | DIGIKEY
Y1 | 1 | 8MHz | Crystal:Crystal_SMD_Abracon_ABM8G-4Pin_3.2x2.5mm
Y2 | 1 | 32.768k | Crystal:Crystal_SMD_2012-2Pin_2.0x1.2mm | ABS06-32.768KHZ-1-T | DIGIKEY
 |  |  |  | PHR-7 | LCSC | <- Mating connectors
 |  |  |  | PHR-6 | LCSC
 |  |  |  | PHR-5 | LCSC
 |  |  |  | PHR-4 | LCSC
 |  |  |  | PHR-3 | LCSC
 |  |  |  | SPH-002T-P0.5L | LCSC
 |  |  |  | 1053071202 (https://www.molex.com/en-us/products/part-detail/1053071202) | DIGIKEY
 |  |  |  | 430250400 | LCSC
 |  |  |  | 430300001 (https://www.lcsc.com/product-detail/Housing-Contact_MOLEX-430300001_C259786.html?s_z=n_43030000) | LCSC
 |  |  |  | 436450300 (https://www.lcsc.com/product-detail/Housings-Wire-To-Board-Wire-To-Wire_MOLEX-436450300_C259740.html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) | LCSC
 |  |  |  | 430251000 (https://www.lcsc.com/product-detail/Housings-Wire-To-Board-Wire-To-Wire_MOLEX-430251000_C259745.html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) | LCSC
 |  |  |  | 1053002100 | DIGIKEY
 |  |  |  | Z-SUBDBAM102A092 | LCSC | <- External connectors

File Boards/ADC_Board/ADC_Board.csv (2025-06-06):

Reference | Value | Footprint | Datasheet | MPN | Qty | DNP | Exclude from BOM | Exclude from Board
C1,C2,C5 | 100n | Capacitor_SMD:C_0402_1005Metric | ~ |  | 3
C3,C4 | 4u7 | Capacitor_SMD:C_0603_1608Metric | ~ |  | 2
C6,C7 | ? | Capacitor_SMD:C_0402_1005Metric | ~ |  | 2 | DNP | Excluded from BOM
C8,C9,C16,C28,C32,C36,C43 | 100n | Capacitor_SMD:C_0603_1608Metric | ~ |  | 7
C10,C12 | 22u | Capacitor_SMD:C_1206_3216Metric | ~ |  | 2
C11,C13,C15 | 10u | Capacitor_SMD:C_0603_1608Metric | ~ |  | 3
C14 | 100u | Capacitor_SMD:CP_Elec_8x10.5 | https://search.kemet.com/download/datasheet/A768KS107M1HLAE030 | A768KS107M1HLAE030 | 1
C17 | 330n | Capacitor_SMD:C_0603_1608Metric | ~ |  | 1
C18,C21,C22,C24,C25,C27,C29,C31,C33,C35,C37,C39,C40,C42 | 390p | Capacitor_SMD:C_0402_1005Metric | ~ |  | 14
C19 | 1u | Capacitor_SMD:C_0603_1608Metric | ~ |  | 1
C20,C23,C26,C30,C34,C38,C41 | 3n9 | Capacitor_SMD:C_0402_1005Metric | ~ |  | 7
D1,D2 | PESD3V3L4UW | Package_TO_SOT_SMD:SOT-665 | https://assets.nexperia.com/documents/data-sheet/PESDXL4UF_G_W.pdf |  | 2
D3 | 18V | Diode_SMD:D_SOD-323F | https://www.onsemi.com/pdf/datasheet/mm3z9v1b-d.pdf | MM3Z18VB | 1
D4 | 9V 15.4VC | Diode_SMD:D_SOD-123F | https://www.littelfuse.com/assetdocs/tvs-diodes-smf-datasheet?assetguid=7eb8a5b6-bdd0-4561-8f19-0c3cc6f9b2af | SMF9.0CA | 1
D5 | LED_R | LED_SMD:LED_1206_3216Metric | https://optoelectronics.liteon.com/upload/download/DS-22-99-0149/LTST-C150KRKT.pdf | LTST-C150KRKT | 1
D6 | LED_G | LED_SMD:LED_1206_3216Metric | https://optoelectronics.liteon.com/upload/download/DS22-2000-072/LTST-C150KGKT.pdf | LTST-C150KGKT | 1
D7 | LED_B | LED_SMD:LED_1206_3216Metric | https://optoelectronics.liteon.com/upload/download/DS22-2000-026/LTST-C150TBKT(0630).pdf | LTST-C150TBKT | 1
F1 | 2A | Fuse:Fuse_1206_3216Metric | ~ |  | 1
F2 | 2A | Fuse:Fuse_1206_3216Metric | ~ |  | 1 | DNP
FB1 | FerriteBead | Inductor_SMD:L_1206_3216Metric | https://productfinder.pulseelectronics.com/api/open/part-attachments/datasheet/BBUP00321611121Y00 | BBUP00321611121Y00 | 1
H1,H2,H3,H4 | ~ | MountingHole:MountingHole_3.2mm_M3_DIN965_Pad_TopOnly | ~ |  | 4 |  | Excluded from BOM
J1 | SWD JST PH | Connector_JST:JST_PH_B4B-PH-K_1x04_P2.00mm_Vertical | https://www.jst-mfg.com/product/pdf/eng/ePH.pdf | B4B-PH-K-S | 1
J2 | UART JST | Connector_JST:JST_PH_B3B-PH-K_1x03_P2.00mm_Vertical | https://www.jst-mfg.com/product/pdf/eng/ePH.pdf | B3B-PH-K-S | 1
J3 | Extras JST | Connector_JST:JST_PH_B7B-PH-K_1x07_P2.00mm_Vertical | https://www.jst-mfg.com/product/pdf/eng/ePH.pdf | B7B-PH-K-S | 1
J4 | USB_B_Micro | Connector_USB:USB_Micro-B_Amphenol_10118193-0001LF_Horizontal | https://cdn.amphenol-cs.com/media/wysiwyg/files/documentation/datasheet/inputoutput/io_usb_micro.pdf | 10118193-0001LF | 1
J5 | I2CA JST | Connector_JST:JST_PH_B5B-PH-K_1x05_P2.00mm_Vertical | https://www.jst-mfg.com/product/pdf/eng/ePH.pdf | B6B-PH-K-S | 1
J6,J11 | DB9 Microfit | Connector_Dsub:DSUB-9_Pins_Horizontal_P2.77x2.84mm_EdgePinOffset7.70mm_Housed_MountingHolesOffset9.12mm | https://www.molex.com/en-us/products/part-detail/430451027?display=pdf | 0430451027 | 2
J7 | I2CB JST | Connector_JST:JST_PH_B5B-PH-K_1x05_P2.00mm_Vertical | https://www.jst-mfg.com/product/pdf/eng/ePH.pdf | B5B-PH-K-S | 1
J8 | CAN1_T | Connector_PinHeader_2.54mm:PinHeader_1x02_P2.54mm_Vertical | ~ |  | 1 |  | Excluded from BOM
J9 | CAN2_T | Connector_PinHeader_2.54mm:PinHeader_1x02_P2.54mm_Vertical | ~ |  | 1 |  | Excluded from BOM
J10 | I2CC JST | Connector_JST:JST_PH_B5B-PH-K_1x05_P2.00mm_Vertical | https://www.jst-mfg.com/product/pdf/eng/ePH.pdf | B5B-PH-K-S | 1
J12 | Backup Power | Connector_Molex:Molex_Micro-Fit_3.0_43650-0315_1x03_P3.00mm_Vertical | https://www.molex.com/pdm_docs/sd/436500315_sd.pdf | 436500315 | 1
J13 | Load Cell A | Connector_JST:JST_PH_B6B-PH-K_1x06_P2.00mm_Vertical | ~ |  | 1
J14 | Load Cell B | Connector_JST:JST_PH_B6B-PH-K_1x06_P2.00mm_Vertical | ~ |  | 1
J15 | MIPA_A | Connector_JST:JST_PH_B3B-PH-K_1x03_P2.00mm_Vertical | ~ |  | 1
J16 | Load Cell C | Connector_JST:JST_PH_B6B-PH-K_1x06_P2.00mm_Vertical | ~ |  | 1
J17 | MIPA_B | Connector_JST:JST_PH_B3B-PH-K_1x03_P2.00mm_Vertical | ~ |  | 1
J18 | Thermocouple A | Connector_JST:JST_PH_B2B-PH-K_1x02_P2.00mm_Vertical | ~ |  | 1
J19 | MIPA_C | Connector_JST:JST_PH_B3B-PH-K_1x03_P2.00mm_Vertical | ~ |  | 1
J20 | Thermocouple B | Connector_JST:JST_PH_B2B-PH-K_1x02_P2.00mm_Vertical | ~ |  | 1
J21 | Thermocouple C | Connector_JST:JST_PH_B2B-PH-K_1x02_P2.00mm_Vertical | ~ |  | 1
J22 | Cold Juntion Thermistor | Connector_JST:JST_PH_B2B-PH-K_1x02_P2.00mm_Vertical | ~ |  | 1
JP1 | CH SEL | Jumper:SolderJumper-3_P1.3mm_Bridged12_RoundedPad1.0x1.5mm | ~ |  | 1 |  | Excluded from BOM
JP2 | CL SEL | Jumper:SolderJumper-3_P1.3mm_Bridged12_RoundedPad1.0x1.5mm | ~ |  | 1 |  | Excluded from BOM
Q1 | DMP6023LFG | Package_SON:Diodes_PowerDI3333-8 | https://www.diodes.com/assets/Datasheets/DMP6023LFG.pdf | DMP6023LFG-7 | 1
R4,R5 | 27R | Resistor_SMD:R_0603_1608Metric | ~ |  | 2
R6,R8 | 120R | Resistor_SMD:R_0603_1608Metric | ~ |  | 2
R7,R9,R10,R11,R16 | 100K | Resistor_SMD:R_0603_1608Metric | ~ |  | 5
R12 | 14K3 | Resistor_SMD:R_0603_1608Metric | ~ |  | 1
R13 | 549R | Resistor_SMD:R_0603_1608Metric | ~ |  | 1
R14,R15 | 220R | Resistor_SMD:R_0603_1608Metric | ~ |  | 2
R17 | 9K53 | Resistor_SMD:R_0603_1608Metric | ~ |  | 1
R18 | 2R | Resistor_SMD:R_0603_1608Metric | ~ |  | 1
R19,R20,R21,R23,R25,R28,R31,R34,R37,R38,R42,R43,R47,R49 | 2K | Resistor_SMD:R_0402_1005Metric | ~ |  | 14
R22,R24,R26,R27,R30,R32,R33 | 47R | Resistor_SMD:R_0603_1608Metric | ~ |  | 7
R29,R35,R40,R48 | 2K | Resistor_SMD:R_0603_1608Metric | ~ |  | 4
R36,R39,R41,R44,R45,R50 | 1M | Resistor_SMD:R_0402_1005Metric | ~ |  | 6 | DNP
R46 | 20K | Resistor_SMD:R_0603_1608Metric | ~ |  | 1
R51,R52,R53,R54,R55,R56 | 10K | Resistor_SMD:R_0603_1608Metric | ~ |  | 6
TP1 | SYNC | TestPoint:TestPoint_Pad_D1.0mm | ~ |  | 1
TP2 | ADC_RDY | TestPoint:TestPoint_Pad_D1.0mm | ~ |  | 1
TP3 | ADC_RST | TestPoint:TestPoint_Pad_D1.0mm | ~ |  | 1
TP4 | CJT | TestPoint:TestPoint_Pad_D1.0mm | ~ |  | 1
TP5 | MIP1 | TestPoint:TestPoint_Pad_D1.0mm | ~ |  | 1
TP6 | MIP2 | TestPoint:TestPoint_Pad_D1.0mm | ~ |  | 1
TP7 | MIP3 | TestPoint:TestPoint_Pad_D1.0mm | ~ |  | 1
TP8 | CS | TestPoint:TestPoint_Pad_D1.0mm | ~ |  | 1
TP9 | SCK | TestPoint:TestPoint_Pad_D1.0mm | ~ |  | 1
TP10 | MISO | TestPoint:TestPoint_Pad_D1.0mm | ~ |  | 1
TP11 | MOSI | TestPoint:TestPoint_Pad_D1.0mm | ~ |  | 1
TP12 | A9 | TestPoint:TestPoint_Pad_D1.0mm | ~ |  | 1
TP13 | CANRX1 | TestPoint:TestPoint_Pad_D1.0mm | ~ |  | 1
TP14 | CANTX1 | TestPoint:TestPoint_Pad_D1.0mm | ~ |  | 1
TP15 | A11 | TestPoint:TestPoint_Pad_D1.0mm | ~ |  | 1
TP16 | 7.4V | TestPoint:TestPoint_Pad_D1.0mm | ~ |  | 1
TP17 | 5V | TestPoint:TestPoint_Pad_D1.0mm | ~ |  | 1
TP18 | 3.3V | TestPoint:TestPoint_Pad_D1.0mm | ~ |  | 1
TP19,TP20 | GND | TestPoint:TestPoint_Bridge_Pitch2.54mm_Drill1.3mm | ~ |  | 2
TP29 | AINCOM | TestPoint:TestPoint_Pad_1.5x1.5mm | ~ |  | 1
U1 | STM32G0B1RCTx | Package_QFP:LQFP-64_10x10mm_P0.5mm | https://www.st.com/resource/en/datasheet/stm32g0b1rc.pdf | STM32G0B1RCT6 | 1
U2 | TCAN1046 | Custom:SOT23_DYY_TEX | https://www.ti.com/lit/ds/symlink/tcan1046av-q1.pdf | TCAN1046AVDYYRQ1 | 1
U3 | AZ1117C-3.3 | Package_TO_SOT_SMD:SOT-223-3_TabPin2 | https://www.diodes.com/assets/Datasheets/AZ1117C.pdf | AZ1117CH-3.3TRG1 | 1
U4 | AZ1117C-5.0 | Package_TO_SOT_SMD:SOT-223-3_TabPin2 | https://www.diodes.com/assets/Datasheets/AZ1117C.pdf | AZ1117CH-5.0TRG1 | 1
U5 | ADS124S08IRHBR | Package_QFP:LQFP-32_5x5mm_P0.5mm | https://www.ti.com/lit/ds/symlink/ads124s06.pdf?HQS=dis-dk-null-digikeymode-dsf-pf-null-wwe&ts=1745919423415 | ADS124S08IRHBR | 1
Y1 | 8MHz | Crystal:Crystal_SMD_Abracon_ABM8G-4Pin_3.2x2.5mm | ~ |  | 1 | DNP | Excluded from BOM

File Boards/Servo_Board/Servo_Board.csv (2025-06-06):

Reference | Value | Footprint | Datasheet | Qty | MPN | DNP | Exclude from BOM | Exclude from Board
C1,C2,C5 | 100n | Capacitor_SMD:C_0402_1005Metric | ~ | 3
C3,C4 | 4u7 | Capacitor_SMD:C_0603_1608Metric | ~ | 2
C6,C7 | ? | Capacitor_SMD:C_0402_1005Metric | ~ | 2 |  | DNP | Excluded from BOM
C8,C9,C10,C16,C19,C20,C23 | 100n | Capacitor_SMD:C_0603_1608Metric | ~ | 7
C11,C13 | 22u | Capacitor_SMD:C_1206_3216Metric | ~ | 2
C12,C14 | 10u | Capacitor_SMD:C_0603_1608Metric | ~ | 2
C15,C17,C21,C22 | 100u | Capacitor_SMD:CP_Elec_6.3x5.9 | https://aishi.us/files/VZ.pdf | 4 | SVZ1CM101E06E00RAXXX
D1 | LED_B | LED_SMD:LED_1206_3216Metric | https://optoelectronics.liteon.com/upload/download/DS-22-99-0149/LTST-C150KRKT.pdf | 1 | LTST-C150KRKT
D2 | LED_G | LED_SMD:LED_1206_3216Metric | https://optoelectronics.liteon.com/upload/download/DS22-2000-072/LTST-C150KGKT.pdf | 1 | LTST-C150KGKT
D3 | LED_R | LED_SMD:LED_1206_3216Metric | https://optoelectronics.liteon.com/upload/download/DS22-2000-026/LTST-C150TBKT(0630).pdf | 1 | LTST-C150TBKT
D4,D5 | PESD3V3L4UW | Package_TO_SOT_SMD:SOT-665 | https://assets.nexperia.com/documents/data-sheet/PESDXL4UF_G_W.pdf | 2
D6 | 18V | Diode_SMD:D_SOD-323F | https://www.onsemi.com/pdf/datasheet/mm3z9v1b-d.pdf | 1 | MM3Z18VB
D7,D10 | 9V 15.4VC | Diode_SMD:D_SOD-123F | https://www.littelfuse.com/assetdocs/tvs-diodes-smf-datasheet?assetguid=7eb8a5b6-bdd0-4561-8f19-0c3cc6f9b2af | 2 | SMF9.0CA
D8 | D_0.5VF | Diode_SMD:D_SOD-523 | https://www.onsemi.com/pdf/datasheet/rb521s30t1-d.pdf | 1 | RB521S30T5G
D9 | 2.5V Ref Zener | Package_TO_SOT_SMD:SOT-23-3 | ~ | 1 | LM4040CYM3-2.5-TR
F1,F2 | 5A | Fuse:Fuse_1206_3216Metric | ~ | 2
H1,H2,H3,H4 | ~ | MountingHole:MountingHole_3.2mm_M3_DIN965_Pad_TopOnly | ~ | 4 |  |  | Excluded from BOM
J1 | SWD JST PH | Connector_JST:JST_PH_B4B-PH-K_1x04_P2.00mm_Vertical | https://www.jst-mfg.com/product/pdf/eng/ePH.pdf | 1 | B4B-PH-K-S
J2 | UART JST | Connector_JST:JST_PH_B3B-PH-K_1x03_P2.00mm_Vertical | https://www.jst-mfg.com/product/pdf/eng/ePH.pdf | 1 | B3B-PH-K-S
J3,J18 | Extras JST | Connector_JST:JST_PH_B7B-PH-K_1x07_P2.00mm_Vertical | https://www.jst-mfg.com/product/pdf/eng/ePH.pdf | 2 | B7B-PH-K-S
J4 | USB_B_Micro | Connector_USB:USB_Micro-B_Amphenol_10118193-0001LF_Horizontal | https://cdn.amphenol-cs.com/media/wysiwyg/files/documentation/datasheet/inputoutput/io_usb_micro.pdf | 1 | 10118193-0001LF
J5 | I2CA JST | Connector_JST:JST_PH_B5B-PH-K_1x05_P2.00mm_Vertical | https://www.jst-mfg.com/product/pdf/eng/ePH.pdf | 1 | B6B-PH-K-S
J6,J12 | DB9 Microfit | Connector_Dsub:DSUB-9_Pins_Horizontal_P2.77x2.84mm_EdgePinOffset7.70mm_Housed_MountingHolesOffset9.12mm | https://www.molex.com/en-us/products/part-detail/430451027?display=pdf | 2 | 0430451027
J7 | I2CB JST | Connector_JST:JST_PH_B5B-PH-K_1x05_P2.00mm_Vertical | https://www.jst-mfg.com/product/pdf/eng/ePH.pdf | 1 | B5B-PH-K-S
J8 | SPI JST | Connector_JST:JST_PH_B6B-PH-K_1x06_P2.00mm_Vertical | ~ | 1
J9 | CAN1_T | Connector_PinHeader_2.54mm:PinHeader_1x02_P2.54mm_Vertical | ~ | 1 |  |  | Excluded from BOM
J10 | CAN2_T | Connector_PinHeader_2.54mm:PinHeader_1x02_P2.54mm_Vertical | ~ | 1 |  |  | Excluded from BOM
J11 | I2CC JST | Connector_JST:JST_PH_B5B-PH-K_1x05_P2.00mm_Vertical | https://www.jst-mfg.com/product/pdf/eng/ePH.pdf | 1 | B5B-PH-K-S
J14 | SERVO B | Connector_Molex:Molex_Micro-Fit_3.0_43045-0412_2x02_P3.00mm_Vertical | ~ | 1 | 0430450412
J15 | SERVO A | Connector_Molex:Molex_Micro-Fit_3.0_43045-0412_2x02_P3.00mm_Vertical | ~ | 1 | 0430450412
J16 | SERVO C | Connector_Molex:Molex_Micro-Fit_3.0_43045-0412_2x02_P3.00mm_Vertical | ~ | 1 | 0430450412
J17 | SERVO D | Connector_Molex:Molex_Micro-Fit_3.0_43045-0412_2x02_P3.00mm_Vertical | ~ | 1 | 0430450412
J19 | Backup Power | Connector_Molex:Molex_Micro-Fit_3.0_43650-0315_1x03_P3.00mm_Vertical | https://www.molex.com/pdm_docs/sd/436500315_sd.pdf | 1 | 436500315
JP1 | CH SEL | Jumper:SolderJumper-3_P1.3mm_Bridged12_RoundedPad1.0x1.5mm | ~ | 1 |  |  | Excluded from BOM
JP2 | CL SEL | Jumper:SolderJumper-3_P1.3mm_Bridged12_RoundedPad1.0x1.5mm | ~ | 1 |  |  | Excluded from BOM
Q1 | DMP6023LFG | Package_SON:Diodes_PowerDI3333-8 | https://www.diodes.com/assets/Datasheets/DMP6023LFG.pdf | 1 | DMP6023LFG-7
R1 | 549R | Resistor_SMD:R_0603_1608Metric | ~ | 1
R2,R3 | 220R | Resistor_SMD:R_0603_1608Metric | ~ | 2
R4,R5,R6,R28,R29,R30 | 10K | Resistor_SMD:R_0603_1608Metric | ~ | 6
R7,R8 | 27R | Resistor_SMD:R_0603_1608Metric | ~ | 2
R9,R11 | 120R | Resistor_SMD:R_0603_1608Metric | ~ | 2
R10,R12,R13,R14,R18 | 100K | Resistor_SMD:R_0603_1608Metric | ~ | 5
R15,R16,R20,R21 | 100k | Resistor_SMD:R_0603_1608Metric | ~ | 4
R17 | 14K3 | Resistor_SMD:R_0603_1608Metric | ~ | 1
R19 | 9K53 | Resistor_SMD:R_0603_1608Metric | ~ | 1
R22 | 22K | Resistor_SMD:R_0603_1608Metric | ~ | 1
R23 | 15K | Resistor_SMD:R_0603_1608Metric | ~ | 1
R24 | 6K2 | Resistor_SMD:R_0603_1608Metric | ~ | 1
R25 | 4K7 | Resistor_SMD:R_0603_1608Metric | ~ | 1
R26 | 1K5 | Resistor_SMD:R_0603_1608Metric | ~ | 1
R27 | R | Resistor_SMD:R_0603_1608Metric | ~ | 1 |  | DNP | Excluded from BOM
SW1 | On Switch | Connector_Molex:Molex_Micro-Fit_3.0_43650-0215_1x02_P3.00mm_Vertical | https://tools.molex.com/pdm_docs/ps/PS-43650.pdf | 1 | 436500228
TP1 | CANRX1 | TestPoint:TestPoint_Pad_D1.0mm | ~ | 1
TP2 | CANTX1 | TestPoint:TestPoint_Pad_D1.0mm | ~ | 1
TP3 | 2S+ | TestPoint:TestPoint_Pad_D1.0mm | ~ | 1
TP4 | P_SOURCE | TestPoint:TestPoint_Pad_D1.0mm | ~ | 1
TP16 | 7.4V | TestPoint:TestPoint_Pad_D1.0mm | ~ | 1
TP17 | 5V | TestPoint:TestPoint_Pad_D1.0mm | ~ | 1
TP18 | 3.3V | TestPoint:TestPoint_Pad_D1.0mm | ~ | 1
TP19,TP20 | GND | TestPoint:TestPoint_Bridge_Pitch2.54mm_Drill1.3mm | ~ | 2
U1 | STM32G0B1RCTx | Package_QFP:LQFP-64_10x10mm_P0.5mm | https://www.st.com/resource/en/datasheet/stm32g0b1rc.pdf | 1 | STM32G0B1RCT6
U2 | TCAN1046 | Custom:SOT23_DYY_TEX | https://www.ti.com/lit/ds/symlink/tcan1046av-q1.pdf | 1 | TCAN1046AVDYYRQ1
U3 | AZ1117C-3.3 | Package_TO_SOT_SMD:SOT-223-3_TabPin2 | https://www.diodes.com/assets/Datasheets/AZ1117C.pdf | 1 | AZ1117CH-3.3TRG1
U4 | AZ1117C-5.0 | Package_TO_SOT_SMD:SOT-223-3_TabPin2 | https://www.diodes.com/assets/Datasheets/AZ1117C.pdf | 1 | AZ1117CH-5.0TRG1
U5 | TPS2121RUXR | Custom:RUX0012A | https://www.ti.com/lit/ds/symlink/tps2120.pdf | 1 | TPS2121RUXR
Y1 | 8MHz | Crystal:Crystal_SMD_Abracon_ABM8G-4Pin_3.2x2.5mm | ~ | 1 |  | DNP | Excluded from BOM

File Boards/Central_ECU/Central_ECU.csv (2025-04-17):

Reference | Qty | Value | Footprint | Datasheet | MPN
C1,C4,C37,C39 | 4 | 10u | Capacitor_SMD:C_0603_1608Metric | ~
C2,C3,C13,C14,C15,C17,C18,C25,C29,C32,C35,C42 | 12 | 100n | Capacitor_SMD:C_0603_1608Metric | ~
C5 | 1 | 100m | Capacitor_THT:CP_Radial_D14.0mm_P5.00mm | https://mm.digikey.com/Volume0/opasdata/d220001/medias/docus/6448/DB%2C%20DBN%20Series.pdf | RSCBN1045R5G07014T
C6,C8,C9 | 3 | 100n | Capacitor_SMD:C_0402_1005Metric | ~
C7,C10,C16 | 3 | 4u7 | Capacitor_SMD:C_0603_1608Metric | ~
C11,C12 | 2 | ? | Capacitor_SMD:C_0402_1005Metric | ~
C19,C20 | 2 | 12p | Capacitor_SMD:C_0402_1005Metric | ~
C23,C24 | 2 | 22u | Capacitor_SMD:C_0603_1608Metric | ~
C26 | 1 | 10u | Capacitor_SMD:C_1206_3216Metric | ~
C27,C30,C31,C33,C34,C38,C40 | 7 | 22u | Capacitor_SMD:C_1206_3216Metric | ~
C28 | 1 | ? | Capacitor_SMD:C_0603_1608Metric | ~
C36,C41,C43 | 3 | 100u | Capacitor_SMD:CP_Elec_8x10.5 | https://search.kemet.com/download/datasheet/A768KS107M1HLAE030 | A768KS107M1HLAE030
CR1 | 1 | ST490ABDR | Package_SO:SO-8_3.9x4.9mm_P1.27mm | https://www.st.com/content/ccc/resource/technical/document/datasheet/45/b4/14/d4/eb/dc/4a/7e/CD00003152.pdf/files/CD00003152.pdf/jcr:content/translations/en.C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 | ST490ABDR
D1,D5,D11 | 3 | D_Schottky | Diode_SMD:D_SOD-882 | https://toshiba.semicon-storage.com/info/docget.jsp?did=14192&prodName=CTS05S40 | CTS05S40,L3F
D2 | 1 | LED_R | LED_SMD:LED_1206_3216Metric | https://optoelectronics.liteon.com/upload/download/DS-22-99-0149/LTST-C150KRKT.pdf | LTST-C150KRKT
D3 | 1 | LED_G | LED_SMD:LED_1206_3216Metric | https://optoelectronics.liteon.com/upload/download/DS22-2000-072/LTST-C150KGKT.pdf | LTST-C150KGKT
D4 | 1 | LED_B | LED_SMD:LED_1206_3216Metric | https://optoelectronics.liteon.com/upload/download/DS22-2000-026/LTST-C150TBKT(0630).pdf | LTST-C150TBKT
D7,D15 | 2 | TVS 30V | Diode_SMD:D_SOD-882 | https://assets.nexperia.com/documents/data-sheet/PESD1CANFD30L-Q.pdf | PESD1CANFD30L-QYL
D8,D10,D16 | 3 | 30V 34VC | Diode_SMD:D_SOD-882 | https://assets.nexperia.com/documents/data-sheet/PESD1CANFD30L-Q.pdf | PESD1CANFD30L-QYL
D9,D14 | 2 | 18V | Diode_SMD:D_SOD-323F | https://www.onsemi.com/pdf/datasheet/mm3z9v1b-d.pdf | MM3Z18VB
D12 | 1 | PESD3V3L4UW | Package_TO_SOT_SMD:SOT-665 | https://assets.nexperia.com/documents/data-sheet/PESDXL4UF_G_W.pdf | PESD3V3L4UW,115
D13 | 1 | 9V 15.4VC | Diode_SMD:D_SOD-123F | https://www.littelfuse.com/assetdocs/tvs-diodes-smf-datasheet?assetguid=7eb8a5b6-bdd0-4561-8f19-0c3cc6f9b2af | SMF9.0CA
F1 | 1 | 2A | Fuse:Fuse_1206_3216Metric | ~
F2 | 1 | 4A | Fuse:Fuse_1206_3216Metric | ~
F3 | 1 | 5A | Fuse:Fuse_1206_3216Metric | ~
H1,H2,H3,H4 | 4 | ~ | MountingHole:MountingHole_3.2mm_M3_DIN965_Pad_TopOnly | ~
J1 | 1 | Micro_SD_Card | Connector_Card:microSD_HC_Molex_47219-2001 | https://www.molex.com/en-us/products/part-detail/472192001?display=pdf | 0472192001
J2 | 1 | Extras JST | Connector_JST:JST_PH_B7B-PH-K_1x07_P2.00mm_Vertical | https://www.jst-mfg.com/product/pdf/eng/ePH.pdf | B7B-PH-K-S
J3,J6,J16 | 3 | MICROFIT | Connector_Molex:Molex_Micro-Fit_3.0_43045-0412_2x02_P3.00mm_Vertical | https://www.molex.com/pdm_docs/sd/430450412_sd.pdf,~ | 0430450412
J4 | 1 | Siren MICROFIT | Connector_Molex:Molex_Micro-Fit_3.0_43650-0315_1x03_P3.00mm_Vertical | https://www.molex.com/pdm_docs/sd/436500315_sd.pdf | 436500315
J5 | 1 | I2CB JST | Connector_JST:JST_PH_B5B-PH-K_1x05_P2.00mm_Vertical | https://www.jst-mfg.com/product/pdf/eng/ePH.pdf | B6B-PH-K-S
J7 | 1 | I2CA JST | Connector_JST:JST_PH_B5B-PH-K_1x05_P2.00mm_Vertical | https://www.jst-mfg.com/product/pdf/eng/ePH.pdf | B5B-PH-K-S
J8 | 1 | Ignitor JST EH | Connector_JST:JST_EH_B4B-EH-A_1x04_P2.50mm_Vertical | https://www.jst-mfg.com/product/pdf/eng/ePH.pdf | B4B-PH-K-S
J9 | 1 | DB9 MICROFIT | Connector_Molex:Molex_Micro-Fit_3.0_43045-1012_2x05_P3.00mm_Vertical | https://www.molex.com/en-us/products/part-detail/430451027?display=pdf | 0430451027
J10 | 1 | Solenoid NANOFIT | Connector_Molex:Molex_Nano-Fit_105309-xx02_1x02_P2.50mm_Vertical | https://tools.molex.com/pdm_docs/ps/PS-105300-100-001.pdf | 1053091102
J11 | 1 | DB9 Microfit | Connector_Molex:Molex_Micro-Fit_3.0_43045-1012_2x05_P3.00mm_Vertical | https://www.molex.com/en-us/products/part-detail/430451027?display=pdf | 0430451027
J12 | 1 | RS422 JST | Connector_JST:JST_PH_B6B-PH-K_1x06_P2.00mm_Vertical | https://www.jst-mfg.com/product/pdf/eng/ePH.pdf | B6B-PH-K-S
J13 | 1 | USB_B_Micro | Connector_USB:USB_Micro-B_Amphenol_10118193-0001LF_Horizontal | https://cdn.amphenol-cs.com/media/wysiwyg/files/documentation/datasheet/inputoutput/io_usb_micro.pdf | 10118193-0001LF
J14 | 1 | SWD JST PH | Connector_JST:JST_PH_B4B-PH-K_1x04_P2.00mm_Vertical | https://www.jst-mfg.com/product/pdf/eng/ePH.pdf | B4B-PH-K-S
J15 | 1 | UART JST | Connector_JST:JST_PH_B3B-PH-K_1x03_P2.00mm_Vertical | https://www.jst-mfg.com/product/pdf/eng/ePH.pdf | B3B-PH-K-S
Q1,Q2,Q3 | 3 | DMT12H060LFDF | Package_DFN_QFN:Diodes_UDFN2020-6_Type-F | https://www.diodes.com/assets/Datasheets/DMT12H060LFDF.pdf | DMT12H060LFDF-7
Q4,Q5 | 2 | DMP6023LFG | Package_SON:Diodes_PowerDI3333-8 | https://www.diodes.com/assets/Datasheets/DMP6023LFG.pdf | DMP6023LFG-7
R1 | 1 | 33R | Resistor_SMD:R_0603_1608Metric | ~
R2,R3,R4,R5,R32,R34,R36,R38 | 8 | 20K | Resistor_SMD:R_0603_1608Metric | ~
R6,R7 | 2 | 27R | Resistor_SMD:R_0603_1608Metric | ~
R8,R9,R10,R12 | 4 | 60R | Resistor_SMD:R_0603_1608Metric | ~
R11 | 1 | 100R | Resistor_SMD:R_0603_1608Metric | ~
R13 | 1 | 330R | Resistor_SMD:R_0603_1608Metric | ~
R14 | 1 | 220R | Resistor_SMD:R_0603_1608Metric | ~
R15 | 1 | 1K | Resistor_SMD:R_0603_1608Metric | ~
R16,R17,R18,R19,R28,R49,R50,R51,R52 | 9 | 10K | Resistor_SMD:R_0603_1608Metric | ~
R20,R23 | 2 | 0R | Resistor_SMD:R_1206_3216Metric | ~
R21,R22 | 2 | 0R | Resistor_SMD:R_1206_3216Metric | ~
R25,R33,R37 | 3 | 549 | Resistor_SMD:R_0603_1608Metric | ~
R26,R35,R39 | 3 | 3.3K | Resistor_SMD:R_0603_1608Metric | ~
R27 | 1 | 2K | Resistor_SMD:R_0603_1608Metric | ~
R29 | 1 | 35K7 | Resistor_SMD:R_0603_1608Metric | ~
R30 | 1 | 10k | Resistor_SMD:R_0603_1608Metric | ~
R31 | 1 | 6K2 | Resistor_SMD:R_0603_1608Metric | ~
R40 | 1 | 0R | Resistor_SMD:R_0603_1608Metric | ~
R41,R42 | 2 | 0R | Resistor_SMD:R_0603_1608Metric | ~
R43,R46 | 2 | 100K | Resistor_SMD:R_0603_1608Metric | ~
R44 | 1 | 10K2 | Resistor_SMD:R_0603_1608Metric | ~
R45 | 1 | 2K49 | Resistor_SMD:R_0603_1608Metric | ~
R47 | 1 | 14K3 | Resistor_SMD:R_0603_1608Metric | ~
R48 | 1 | 9K53 | Resistor_SMD:R_0603_1608Metric | ~
SW1 | 1 | Arm Switch | Connector_Molex:Molex_Micro-Fit_3.0_43650-0215_1x02_P3.00mm_Vertical | https://tools.molex.com/pdm_docs/ps/PS-43650.pdf | 436500228
SW2 | 1 | On Switch | Connector_Molex:Molex_Micro-Fit_3.0_43650-0215_1x02_P3.00mm_Vertical | https://tools.molex.com/pdm_docs/ps/PS-43650.pdf | 436500228
TP1 | 1 | RTC_CAP | TestPoint:TestPoint_Pad_1.5x1.5mm | ~
TP2 | 1 | ADC4S | TestPoint:TestPoint_Pad_1.5x1.5mm | ~
TP3 | 1 | ADC2S | TestPoint:TestPoint_Pad_1.5x1.5mm | ~
TP4 | 1 | SPISCK | TestPoint:TestPoint_Pad_1.5x1.5mm | ~
TP5 | 1 | SPIMISO | TestPoint:TestPoint_Pad_1.5x1.5mm | ~
TP6 | 1 | SPIMOSI | TestPoint:TestPoint_Pad_1.5x1.5mm | ~
TP7 | 1 | SPICS | TestPoint:TestPoint_Pad_1.5x1.5mm | ~
TP8 | 1 | CANTX1 | TestPoint:TestPoint_Pad_1.5x1.5mm | ~
TP9 | 1 | CANRX1 | TestPoint:TestPoint_Pad_1.5x1.5mm | ~
TP10 | 1 | CANTX2 | TestPoint:TestPoint_Pad_1.5x1.5mm | ~
TP11 | 1 | CANRX2 | TestPoint:TestPoint_Pad_1.5x1.5mm | ~
TP12 | 1 | CONT2 | TestPoint:TestPoint_Pad_1.5x1.5mm | ~
TP13 | 1 | CONT1 | TestPoint:TestPoint_Pad_1.5x1.5mm | ~
TP14 | 1 | RS422TX | TestPoint:TestPoint_Pad_1.5x1.5mm | ~
TP15 | 1 | OXSNE | TestPoint:TestPoint_Pad_1.5x1.5mm | ~
TP16 | 1 | RS422RX | TestPoint:TestPoint_Pad_1.5x1.5mm | ~
TP17 | 1 | SNE12 | TestPoint:TestPoint_Pad_1.5x1.5mm | ~
TP18 | 1 | OXFIRE | TestPoint:TestPoint_Pad_1.5x1.5mm | ~
TP19 | 1 | EMCH2 | TestPoint:TestPoint_Pad_1.5x1.5mm | ~
TP20 | 1 | EMCH1 | TestPoint:TestPoint_Pad_1.5x1.5mm | ~
TP21 | 1 | ARMSIG | TestPoint:TestPoint_Pad_1.5x1.5mm | ~
TP22 | 1 | IMON | TestPoint:TestPoint_Pad_1.5x1.5mm | ~
TP23 | 1 | PGOOD | TestPoint:TestPoint_Pad_1.5x1.5mm | ~
TP24 | 1 | 7.4V | TestPoint:TestPoint_Pad_1.5x1.5mm | ~
TP25 | 1 | 5V | TestPoint:TestPoint_Pad_1.5x1.5mm | ~
TP26 | 1 | 3.3V | TestPoint:TestPoint_Pad_1.5x1.5mm | ~
TP27,TP28 | 2 | GND | TestPoint:TestPoint_Bridge_Pitch2.54mm_Drill1.3mm | ~
TP29 | 1 | SPICY+ | TestPoint:TestPoint_Pad_1.5x1.5mm | ~
TP30 | 1 | ARMED | TestPoint:TestPoint_Pad_1.5x1.5mm | ~
TP31 | 1 | ADC2 | TestPoint:TestPoint_Pad_1.5x1.5mm | ~
TP32 | 1 | ADC3 | TestPoint:TestPoint_Pad_1.5x1.5mm | ~
U1 | 1 | SSD1306 | Custom:SSD1306-0.91-OLED-4pin-128x32 |  | N/A
U2 | 1 | STM32G0B1RCTx | Package_QFP:LQFP-64_10x10mm_P0.5mm | https://www.st.com/resource/en/datasheet/stm32g0b1rc.pdf | STM32G0B1RCT6
U3 | 1 | TCAN1046 | Custom:SOT23_DYY_TEX | https://www.ti.com/lit/ds/symlink/tcan1046av-q1.pdf | TCAN1046AVDYYRQ1
U4 | 1 | LM339B | Package_SO:TSSOP-14_4.4x5mm_P0.65mm | https://www.ti.com/lit/ds/symlink/lm2901b.pdf?ts=1695229373008 | LM339BIPWR
U6 | 1 | TPS16630PWPR | Package_SO:HTSSOP-20-1EP_4.4x6.5mm_P0.65mm_EP3.4x6.5mm_Mask2.96x2.96mm_ThermalVias | https://www.ti.com/lit/ds/symlink/tps1663.pdf?HQS=dis-dk-null-digikeymode-dsf-pf-null-wwe&ts=1719393118316 | TPS16630PWPR
U7 | 1 | AZ1117C-5.0 | Package_TO_SOT_SMD:SOT-223-3_TabPin2 | https://www.diodes.com/assets/Datasheets/AZ1117C.pdf | AZ1117CH-5.0TRG1
U8 | 1 | AZ1117C-3.3 | Package_TO_SOT_SMD:SOT-223-3_TabPin2 | https://www.diodes.com/assets/Datasheets/AZ1117C.pdf | AZ1117CH-3.3TRG1
U9 | 1 | LPS22HH | Package_LGA:ST_HLGA-10_2x2mm_P0.5mm_LayoutBorder3x2y | https://www.st.com/resource/en/datasheet/lps22hh.pdf | LPS22HHTR
Y1 | 1 | 8MHz | Crystal:Crystal_SMD_Abracon_ABM8G-4Pin_3.2x2.5mm | ~
Y2 | 1 | 32.768k | Crystal:Crystal_SMD_2012-2Pin_2.0x1.2mm | https://abracon.com/Resonators/ABS06.pdf | ABS06-32.768KHZ-1-T

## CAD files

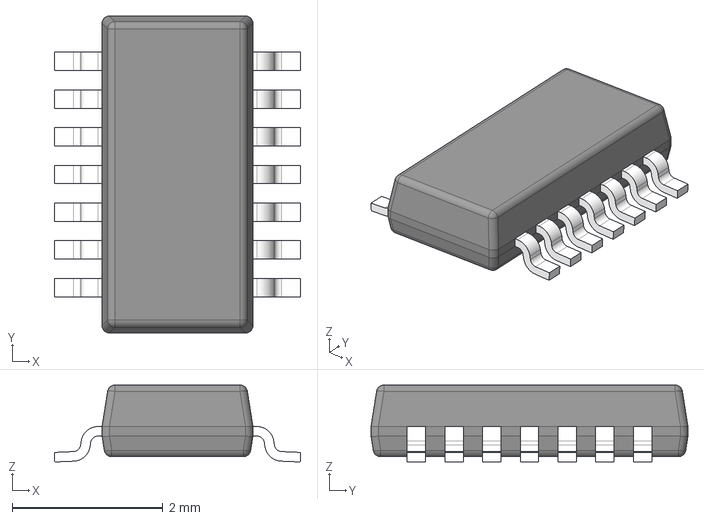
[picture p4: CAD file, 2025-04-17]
Boards/CAD_Models/DYY0014A.stp
3.26 x 4.20 x 1.02 mm
BODY-TSSOP
LEAD-TSSOP x 14

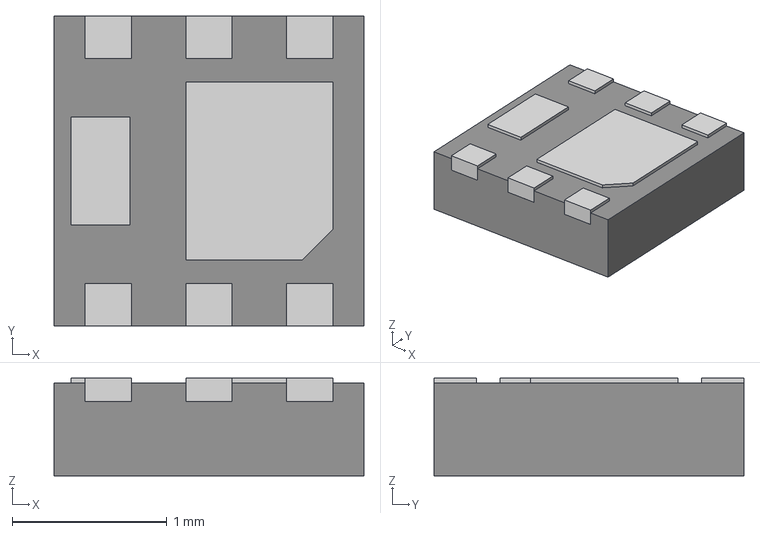
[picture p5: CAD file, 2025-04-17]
Boards/CAD_Models/U-DFN2020-6.step
2.00 x 2.00 x 0.63 mm
Contacts
MainBody

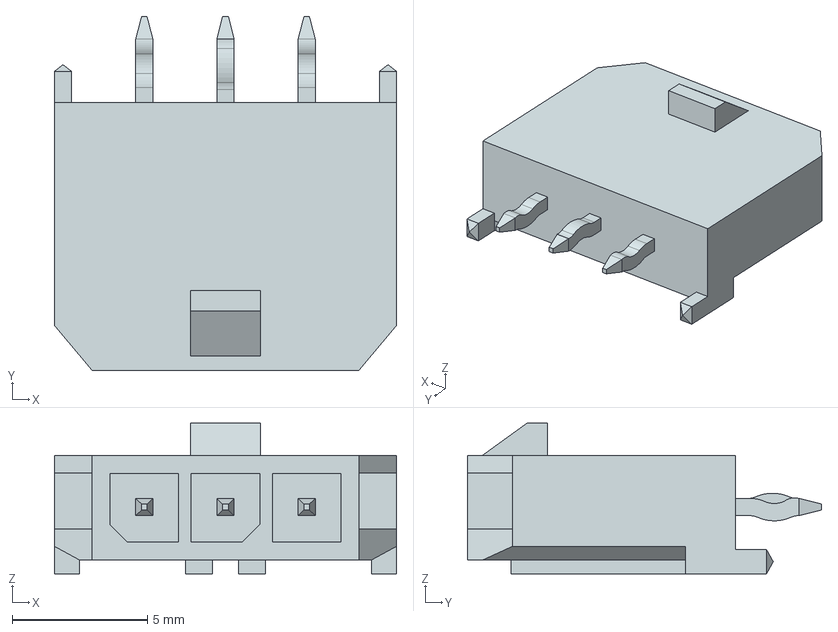
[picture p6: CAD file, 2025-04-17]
Boards/CAD_Models/436500315.stp
12.7 x 13.1 x 5.57 mm

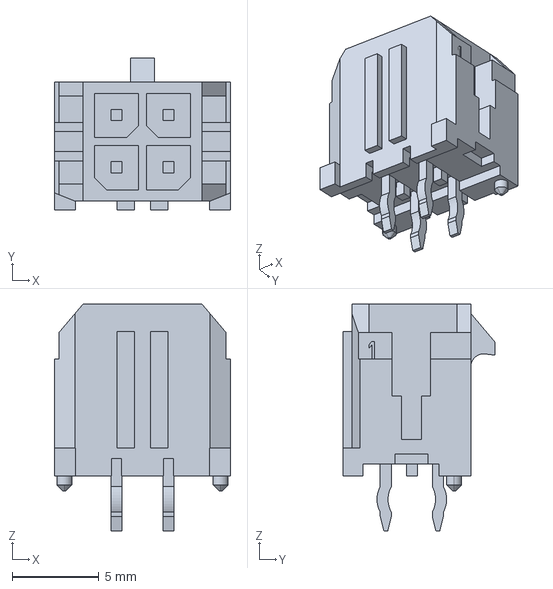
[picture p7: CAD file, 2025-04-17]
Boards/CAD_Models/0430450412.stp
10.2 x 8.77 x 13.1 mm

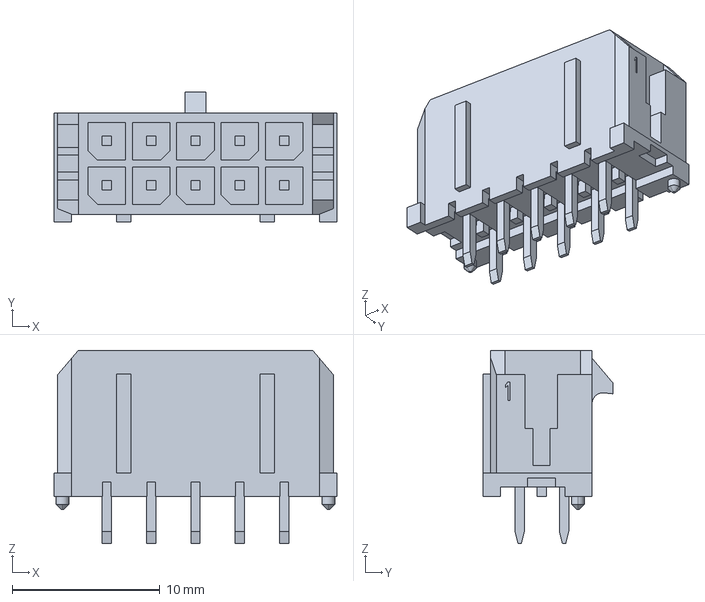
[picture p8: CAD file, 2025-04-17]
Boards/CAD_Models/0430451027.stp
19.1 x 8.77 x 13.1 mm

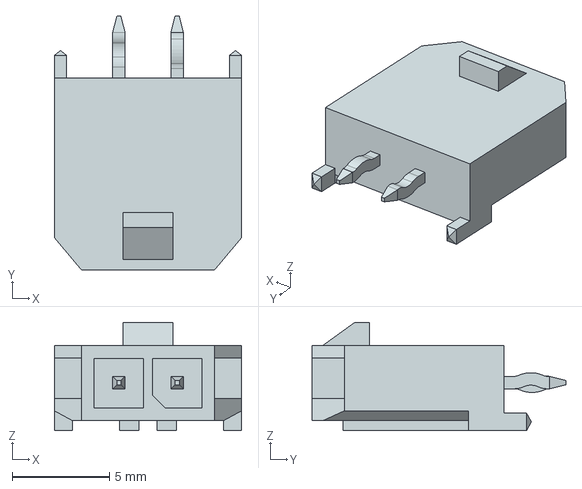
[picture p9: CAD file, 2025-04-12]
Boards/CAD_Models/436500215.stp
9.65 x 13.1 x 5.57 mm

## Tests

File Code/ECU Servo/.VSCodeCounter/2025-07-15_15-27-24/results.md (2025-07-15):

# Summary

Date : 2025-07-15 15:27:24

Directory /Users/bradr/Uni/FYP/Hybrid25_ECU/Code/ECU Servo

Total : 161 files,  93055 codes, 75724 comments, 24840 blanks, all 193619 lines

Summary / [Details](details.md) / [Diff Summary](diff.md) / [Diff Details](diff-details.md)

## Languages
| language | files | code | comment | blank | total |
| :--- | ---: | ---: | ---: | ---: | ---: |
| C++ | 97 | 59,237 | 51,487 | 15,540 | 126,264 |
| C | 48 | 32,040 | 24,169 | 9,018 | 65,227 |
| YAML | 1 | 402 | 4 | 36 | 442 |
| JSON | 3 | 358 | 0 | 1 | 359 |
| CMake | 9 | 332 | 0 | 88 | 420 |
| CMake Cache | 1 | 329 | 0 | 73 | 402 |
| Assembly | 1 | 240 | 0 | 57 | 297 |
| LinkerScript | 1 | 117 | 64 | 27 | 208 |

## Directories
| path | files | code | comment | blank | total |
| :--- | ---: | ---: | ---: | ---: | ---: |
| . | 161 | 93,055 | 75,724 | 24,840 | 193,619 |
| . (Files) | 6 | 1,094 | 64 | 166 | 1,324 |
| CMakeFiles | 10 | 2,009 | 127 | 404 | 2,540 |
| CMakeFiles (Files) | 4 | 429 | 4 | 41 | 474 |
| CMakeFiles/4.0.1 | 6 | 1,580 | 123 | 363 | 2,066 |
| CMakeFiles/4.0.1 (Files) | 4 | 182 | 0 | 57 | 239 |
| CMakeFiles/4.0.1/CompilerIdC | 1 | 690 | 61 | 155 | 906 |
| CMakeFiles/4.0.1/CompilerIdCXX | 1 | 708 | 62 | 151 | 921 |
| Core | 9 | 1,235 | 1,140 | 495 | 2,870 |
| Core/Inc | 3 | 251 | 189 | 92 | 532 |
| Core/Src | 6 | 984 | 951 | 403 | 2,338 |
| Drivers | 106 | 84,069 | 72,031 | 22,498 | 178,598 |
| Drivers/CMSIS | 27 | 29,860 | 10,558 | 7,879 | 48,297 |
| Drivers/CMSIS/Device | 3 | 9,859 | 988 | 776 | 11,623 |
| Drivers/CMSIS/Device/ST | 3 | 9,859 | 988 | 776 | 11,623 |
| Drivers/CMSIS/Device/ST/STM32G0xx | 3 | 9,859 | 988 | 776 | 11,623 |
| Drivers/CMSIS/Device/ST/STM32G0xx/Include | 3 | 9,859 | 988 | 776 | 11,623 |
| Drivers/CMSIS/Include | 24 | 20,001 | 9,570 | 7,103 | 36,674 |
| Drivers/STM32G0xx_HAL_Driver | 79 | 54,209 | 61,473 | 14,619 | 130,301 |
| Drivers/STM32G0xx_HAL_Driver/Inc | 49 | 26,624 | 39,945 | 6,965 | 73,534 |
| Drivers/STM32G0xx_HAL_Driver/Inc (Files) | 48 | 23,729 | 39,329 | 6,556 | 69,614 |
| Drivers/STM32G0xx_HAL_Driver/Inc/Legacy | 1 | 2,895 | 616 | 409 | 3,920 |
| Drivers/STM32G0xx_HAL_Driver/Src | 30 | 27,585 | 21,528 | 7,654 | 56,767 |
| Middlewares | 9 | 2,560 | 1,216 | 707 | 4,483 |
| Middlewares/ST | 9 | 2,560 | 1,216 | 707 | 4,483 |
| Middlewares/ST/STM32_USB_Device_Library | 9 | 2,560 | 1,216 | 707 | 4,483 |
| Middlewares/ST/STM32_USB_Device_Library/Class | 2 | 593 | 315 | 172 | 1,080 |
| Middlewares/ST/STM32_USB_Device_Library/Class/CDC | 2 | 593 | 315 | 172 | 1,080 |
| Middlewares/ST/STM32_USB_Device_Library/Class/CDC/Inc | 1 | 85 | 66 | 34 | 185 |
| Middlewares/ST/STM32_USB_Device_Library/Class/CDC/Src | 1 | 508 | 249 | 138 | 895 |
| Middlewares/ST/STM32_USB_Device_Library/Core | 7 | 1,967 | 901 | 535 | 3,403 |
| Middlewares/ST/STM32_USB_Device_Library/Core/Inc | 4 | 463 | 263 | 178 | 904 |
| Middlewares/ST/STM32_USB_Device_Library/Core/Src | 3 | 1,504 | 638 | 357 | 2,499 |
| USB_Device | 8 | 715 | 1,052 | 417 | 2,184 |
| USB_Device/App | 6 | 311 | 646 | 249 | 1,206 |
| USB_Device/Target | 2 | 404 | 406 | 168 | 978 |
| X-CUBE-MEMS1 | 3 | 1,061 | 64 | 85 | 1,210 |
| X-CUBE-MEMS1/Target | 3 | 1,061 | 64 | 85 | 1,210 |
| cmake | 2 | 73 | 0 | 18 | 91 |
| cmake (Files) | 1 | 34 | 0 | 11 | 45 |
| cmake/stm32cubemx | 1 | 39 | 0 | 7 | 46 |
| include | 2 | 72 | 3 | 12 | 87 |
| src | 6 | 167 | 27 | 38 | 232 |
| src (Files) | 2 | 28 | 5 | 9 | 42 |
| src/modules | 4 | 139 | 22 | 29 | 190 |
| src/modules/debug_io | 2 | 67 | 14 | 17 | 98 |
| src/modules/rtc_helper | 2 | 72 | 8 | 12 | 92 |

Summary / [Details](details.md) / [Diff Summary](diff.md) / [Diff Details](diff-details.md)

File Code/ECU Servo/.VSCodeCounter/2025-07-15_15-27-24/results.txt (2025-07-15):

Date : 2025-07-15 15:27:24
Directory : /Users/bradr/Uni/FYP/Hybrid25_ECU/Code/ECU Servo
Total : 161 files,  93055 codes, 75724 comments, 24840 blanks, all 193619 lines

Languages
+--------------+------------+------------+------------+------------+------------+
| language     | files      | code       | comment    | blank      | total      |
+--------------+------------+------------+------------+------------+------------+
| C++          |         97 |     59,237 |     51,487 |     15,540 |    126,264 |
| C            |         48 |     32,040 |     24,169 |      9,018 |     65,227 |
| YAML         |          1 |        402 |          4 |         36 |        442 |
| JSON         |          3 |        358 |          0 |          1 |        359 |
| CMake        |          9 |        332 |          0 |         88 |        420 |
| CMake Cache  |          1 |        329 |          0 |         73 |        402 |
| Assembly     |          1 |        240 |          0 |         57 |        297 |
| LinkerScript |          1 |        117 |         64 |         27 |        208 |
+--------------+------------+------------+------------+------------+------------+

Directories
+-------------------------------------------------------------------------------------------------------------------+------------+------------+------------+------------+------------+
| path                                                                                                              | files      | code       | comment    | blank      | total      |
+-------------------------------------------------------------------------------------------------------------------+------------+------------+------------+------------+------------+
| .                                                                                                                 |        161 |     93,055 |     75,724 |     24,840 |    193,619 |
| . (Files)                                                                                                         |          6 |      1,094 |         64 |        166 |      1,324 |
| CMakeFiles                                                                                                        |         10 |      2,009 |        127 |        404 |      2,540 |
| CMakeFiles (Files)                                                                                                |          4 |        429 |          4 |         41 |        474 |
| CMakeFiles/4.0.1                                                                                                  |          6 |      1,580 |        123 |        363 |      2,066 |
| CMakeFiles/4.0.1 (Files)                                                                                          |          4 |        182 |          0 |         57 |        239 |
| CMakeFiles/4.0.1/CompilerIdC                                                                                      |          1 |        690 |         61 |        155 |        906 |
| CMakeFiles/4.0.1/CompilerIdCXX                                                                                    |          1 |        708 |         62 |        151 |        921 |
| Core                                                                                                              |          9 |      1,235 |      1,140 |        495 |      2,870 |
| Core/Inc                                                                                                          |          3 |        251 |        189 |         92 |        532 |
| Core/Src                                                                                                          |          6 |        984 |        951 |        403 |      2,338 |
| Drivers                                                                                                           |        106 |     84,069 |     72,031 |     22,498 |    178,598 |
| Drivers/CMSIS                                                                                                     |         27 |     29,860 |     10,558 |      7,879 |     48,297 |
| Drivers/CMSIS/Device                                                                                              |          3 |      9,859 |        988 |        776 |     11,623 |
| Drivers/CMSIS/Device/ST                                                                                           |          3 |      9,859 |        988 |        776 |     11,623 |
| Drivers/CMSIS/Device/ST/STM32G0xx                                                                                 |          3 |      9,859 |        988 |        776 |     11,623 |
| Drivers/CMSIS/Device/ST/STM32G0xx/Include                                                                         |          3 |      9,859 |        988 |        776 |     11,623 |
| Drivers/CMSIS/Include                                                                                             |         24 |     20,001 |      9,570 |      7,103 |     36,674 |
| Drivers/STM32G0xx_HAL_Driver                                                                                      |         79 |     54,209 |     61,473 |     14,619 |    130,301 |
| Drivers/STM32G0xx_HAL_Driver/Inc                                                                                  |         49 |     26,624 |     39,945 |      6,965 |     73,534 |
| Drivers/STM32G0xx_HAL_Driver/Inc (Files)                                                                          |         48 |     23,729 |     39,329 |      6,556 |     69,614 |
| Drivers/STM32G0xx_HAL_Driver/Inc/Legacy                                                                           |          1 |      2,895 |        616 |        409 |      3,920 |
| Drivers/STM32G0xx_HAL_Driver/Src                                                                                  |         30 |     27,585 |     21,528 |      7,654 |     56,767 |
| Middlewares                                                                                                       |          9 |      2,560 |      1,216 |        707 |      4,483 |
| Middlewares/ST                                                                                                    |          9 |      2,560 |      1,216 |        707 |      4,483 |
| Middlewares/ST/STM32_USB_Device_Library                                                                           |          9 |      2,560 |      1,216 |        707 |      4,483 |
| Middlewares/ST/STM32_USB_Device_Library/Class                                                                     |          2 |        593 |        315 |        172 |      1,080 |
| Middlewares/ST/STM32_USB_Device_Library/Class/CDC                                                                 |          2 |        593 |        315 |        172 |      1,080 |
| Middlewares/ST/STM32_USB_Device_Library/Class/CDC/Inc                                                             |          1 |         85 |         66 |         34 |        185 |
| Middlewares/ST/STM32_USB_Device_Library/Class/CDC/Src                                                             |          1 |        508 |        249 |        138 |        895 |
| Middlewares/ST/STM32_USB_Device_Library/Core                                                                      |          7 |      1,967 |        901 |        535 |      3,403 |
| Middlewares/ST/STM32_USB_Device_Library/Core/Inc                                                                  |          4 |        463 |        263 |        178 |        904 |
| Middlewares/ST/STM32_USB_Device_Library/Core/Src                                                                  |          3 |      1,504 |        638 |        357 |      2,499 |
| USB_Device                                                                                                        |          8 |        715 |      1,052 |        417 |      2,184 |
| USB_Device/App                                                                                                    |          6 |        311 |        646 |        249 |      1,206 |
| USB_Device/Target                                                                                                 |          2 |        404 |        406 |        168 |        978 |
| X-CUBE-MEMS1                                                                                                      |          3 |      1,061 |         64 |         85 |      1,210 |
| X-CUBE-MEMS1/Target                                                                                               |          3 |      1,061 |         64 |         85 |      1,210 |
| cmake                                                                                                             |          2 |         73 |          0 |         18 |         91 |
| cmake (Files)                                                                                                     |          1 |         34 |          0 |         11 |         45 |
| cmake/stm32cubemx                                                                                                 |          1 |         39 |          0 |          7 |         46 |
| include                                                                                                           |          2 |         72 |          3 |         12 |         87 |
| src                                                                                                               |          6 |        167 |         27 |         38 |        232 |
| src (Files)                                                                                                       |          2 |         28 |          5 |          9 |         42 |
| src/modules                                                                                                       |          4 |        139 |         22 |         29 |        190 |
| src/modules/debug_io                                                                                              |          2 |         67 |         14 |         17 |         98 |
| src/modules/rtc_helper                                                                                            |          2 |         72 |          8 |         12 |         92 |
+-------------------------------------------------------------------------------------------------------------------+------------+------------+------------+------------+------------+

Files
+-------------------------------------------------------------------------------------------------------------------+--------------+------------+------------+------------+------------+
| filename                                                                                                          | language     | code       | comment    | blank      | total      |
+-------------------------------------------------------------------------------------------------------------------+--------------+------------+------------+------------+------------+
| /Users/bradr/Uni/FYP/Hybrid25_ECU/Code/ECU Servo/CMakeCache.txt                                                   | CMake Cache  |        329 |          0 |         73 |        402 |
| /Users/bradr/Uni/FYP/Hybrid25_ECU/Code/ECU Servo/CMakeFiles/4.0.1/CMakeASMCompiler.cmake                          | CMake        |         24 |          0 |          7 |         31 |
| /Users/bradr/Uni/FYP/Hybrid25_ECU/Code/ECU Servo/CMakeFiles/4.0.1/CMakeCCompiler.cmake                            | CMake        |         66 |          0 |         18 |         84 |
| /Users/bradr/Uni/FYP/Hybrid25_ECU/Code/ECU Servo/CMakeFiles/4.0.1/CMakeCXXCompiler.cmake                          | CMake        |         82 |          0 |         26 |        108 |
| /Users/bradr/Uni/FYP/Hybrid25_ECU/Code/ECU Servo/CMakeFiles/4.0.1/CMakeSystem.cmake                               | CMake        |         10 |          0 |          6 |         16 |
| /Users/bradr/Uni/FYP/Hybrid25_ECU/Code/ECU Servo/CMakeFiles/4.0.1/CompilerIdC/CMakeCCompilerId.c                  | C            |        690 |         61 |        155 |        906 |
| /Users/bradr/Uni/FYP/Hybrid25_ECU/Code/ECU Servo/CMakeFiles/4.0.1/CompilerIdCXX/CMakeCXXCompilerId.cpp            | C++          |        708 |         62 |        151 |        921 |
| /Users/bradr/Uni/FYP/Hybrid25_ECU/Code/ECU Servo/CMakeFiles/CMakeConfigureLog.yaml                                | YAML         |        402 |          4 |         36 |        442 |
| /Users/bradr/Uni/FYP/Hybrid25_ECU/Code/ECU Servo/CMakeFiles/InstallScripts.json                                   | JSON         |          8 |          0 |          1 |          9 |
| /Users/bradr/Uni/FYP/Hybrid25_ECU/Code/ECU Servo/CMakeFiles/VerifyGlobs.cmake                                     | CMake        |         12 |          0 |          2 |         14 |
| /Users/bradr/Uni/FYP/Hybrid25_ECU/Code/ECU Servo/CMakeFiles/clean_additional.cmake                                | CMake        |          7 |          0 |          2 |          9 |
| /Users/bradr/Uni/FYP/Hybrid25_ECU/Code/ECU Servo/CMakePresets.json                                                | JSON         |         60 |          0 |          0 |         60 |
| /Users/bradr/Uni/FYP/Hybrid25_ECU/Code/ECU Servo/Core/Inc/main.h                                                  | C++          |         56 |         39 |         21 |        116 |
| /Users/bradr/Uni/FYP/Hybrid25_ECU/Code/ECU Servo/Core/Inc/stm32g0xx_hal_conf.h                                    | C++          |        180 |        116 |         56 |        352 |
| /Users/bradr/Uni/FYP/Hybrid25_ECU/Code/ECU Servo/Core/Inc/stm32g0xx_it.h                                          | C++          |         15 |         34 |         15 |         64 |
| /Users/bradr/Uni/FYP/Hybrid25_ECU/Code/ECU Servo/Core/Src/main.c                                                  | C            |        455 |        237 |        137 |        829 |
| /Users/bradr/Uni/FYP/Hybrid25_ECU/Code/ECU Servo/Core/Src/stm32g0xx_hal_msp.c                                     | C            |        279 |        351 |        159 |        789 |
| /Users/bradr/Uni/FYP/Hybrid25_ECU/Code/ECU Servo/Core/Src/stm32g0xx_it.c                                          | C            |         29 |         96 |         35 |        160 |
| /Users/bradr/Uni/FYP/Hybrid25_ECU/Code/ECU Servo/Core/Src/syscalls.c                                              | C            |        123 |         25 |         29 |        177 |
| /Users/bradr/Uni/FYP/Hybrid25_ECU/Code/ECU Servo/Core/Src/sysmem.c                                                | C            |         24 |         48 |          8 |         80 |
| /Users/bradr/Uni/FYP/Hybrid25_ECU/Code/ECU Servo/Core/Src/system_stm32g0xx.c                                      | C            |         74 |        194 |         35 |        303 |
| /Users/bradr/Uni/FYP/Hybrid25_ECU/Code/ECU Servo/Drivers/CMSIS/Device/ST/STM32G0xx/Include/stm32g0b1xx.h          | C++          |      9,726 |        829 |        719 |     11,274 |
| /Users/bradr/Uni/FYP/Hybrid25_ECU/Code/ECU Servo/Drivers/CMSIS/Device/ST/STM32G0xx/Include/stm32g0xx.h            | C++          |        119 |         89 |         37 |        245 |
| /Users/bradr/Uni/FYP/Hybrid25_ECU/Code/ECU Servo/Drivers/CMSIS/Device/ST/STM32G0xx/Include/system_stm32g0xx.h     | C++          |         14 |         70 |         20 |        104 |
| /Users/bradr/Uni/FYP/Hybrid25_ECU/Code/ECU Servo/Drivers/CMSIS/Include/cmsis_armcc.h                              | C++          |        401 |        355 |        139 |        895 |
| /Users/bradr/Uni/FYP/Hybrid25_ECU/Code/ECU Servo/Drivers/CMSIS/Include/cmsis_armclang.h                           | C++          |        623 |        595 |        227 |      1,445 |
| /Users/bradr/Uni/FYP/Hybrid25_ECU/Code/ECU Servo/Drivers/CMSIS/Include/cmsis_armclang_ltm.h                       | C++          |        948 |        595 |        349 |      1,892 |
| /Users/bradr/Uni/FYP/Hybrid25_ECU/Code/ECU Servo/Drivers/CMSIS/Include/cmsis_compiler.h                           | C++          |        207 |         52 |         25 |        284 |
| /Users/bradr/Uni/FYP/Hybrid25_ECU/Code/ECU Servo/Drivers/CMSIS/Include/cmsis_gcc.h                                | C++          |      1,170 |        620 |        379 |      2,169 |
| /Users/bradr/Uni/FYP/Hybrid25_ECU/Code/ECU Servo/Drivers/CMSIS/Include/cmsis_iccarm.h                             | C++          |        769 |         45 |        151 |        965 |
| /Users/bradr/Uni/FYP/Hybrid25_ECU/Code/ECU Servo/Drivers/CMSIS/Include/cmsis_version.h                            | C++          |         13 |         23 |          4 |         40 |
| /Users/bradr/Uni/FYP/Hybrid25_ECU/Code/ECU Servo/Drivers/CMSIS/Include/core_armv81mml.h                           | C++          |      1,714 |        651 |        604 |      2,969 |
| /Users/bradr/Uni/FYP/Hybrid25_ECU/Code/ECU Servo/Drivers/CMSIS/Include/core_armv8mbl.h                            | C++          |      1,033 |        526 |        363 |      1,922 |
| /Users/bradr/Uni/FYP/Hybrid25_ECU/Code/ECU Servo/Drivers/CMSIS/Include/core_armv8mml.h                            | C++          |      1,627 |        642 |        567 |      2,836 |
| /Users/bradr/Uni/FYP/Hybrid25_ECU/Code/ECU Servo/Drivers/CMSIS/Include/core_cm0.h                                 | C++          |        444 |        327 |        182 |        953 |
| /Users/bradr/Uni/FYP/Hybrid25_ECU/Code/ECU Servo/Drivers/CMSIS/Include/core_cm0plus.h                             | C++          |        528 |        346 |        212 |      1,086 |
| /Users/bradr/Uni/FYP/Hybrid25_ECU/Code/ECU Servo/Drivers/CMSIS/Include/core_cm1.h                                 | C++          |        454 |        338 |        188 |        980 |
| /Users/bradr/Uni/FYP/Hybrid25_ECU/Code/ECU Servo/Drivers/CMSIS/Include/core_cm23.h                                | C++          |      1,081 |        532 |        384 |      1,997 |
| /Users/bradr/Uni/FYP/Hybrid25_ECU/Code/ECU Servo/Drivers/CMSIS/Include/core_cm3.h                                 | C++          |      1,051 |        468 |        419 |      1,938 |
| /Users/bradr/Uni/FYP/Hybrid25_ECU/Code/ECU Servo/Drivers/CMSIS/Include/core_cm33.h                                | C++          |      1,677 |        646 |        588 |      2,911 |
| /Users/bradr/Uni/FYP/Hybrid25_ECU/Code/ECU Servo/Drivers/CMSIS/Include/core_cm35p.h                               | C++          |      1,677 |        646 |        588 |      2,911 |
| /Users/bradr/Uni/FYP/Hybrid25_ECU/Code/ECU Servo/Drivers/CMSIS/Include/core_cm4.h                                 | C++          |      1,182 |        485 |        458 |      2,125 |
| /Users/bradr/Uni/FYP/Hybrid25_ECU/Code/ECU Servo/Drivers/CMSIS/Include/core_cm7.h                                 | C++          |      1,571 |        576 |        579 |      2,726 |
| /Users/bradr/Uni/FYP/Hybrid25_ECU/Code/ECU Servo/Drivers/CMSIS/Include/core_sc000.h                               | C++          |        488 |        335 |        203 |      1,026 |
| /Users/bradr/Uni/FYP/Hybrid25_ECU/Code/ECU Servo/Drivers/CMSIS/Include/core_sc300.h                               | C++          |      1,034 |        467 |        412 |      1,913 |
| /Users/bradr/Uni/FYP/Hybrid25_ECU/Code/ECU Servo/Drivers/CMSIS/Include/mpu_armv7.h                                | C++          |        122 |        125 |         26 |        273 |
| /Users/bradr/Uni/FYP/Hybrid25_ECU/Code/ECU Servo/Drivers/CMSIS/Include/mpu_armv8.h                                | C++          |        168 |        135 |         44 |        347 |
| /Users/bradr/Uni/FYP/Hybrid25_ECU/Code/ECU Servo/Drivers/CMSIS/Include/tz_context.h                               | C++          |         19 |         40 |         12 |         71 |
| /Users/bradr/Uni/FYP/Hybrid25_ECU/Code/ECU Servo/Drivers/STM32G0xx_HAL_Driver/Inc/Legacy/stm32_hal_legacy.h       | C++          |      2,895 |        616 |        409 |      3,920 |
| /Users/bradr/Uni/FYP/Hybrid25_ECU/Code/ECU Servo/Drivers/STM32G0xx_HAL_Driver/Inc/stm32g0xx_hal.h                 | C++          |        460 |        268 |        111 |        839 |
| /Users/bradr/Uni/FYP/Hybrid25_ECU/Code/ECU Servo/Drivers/STM32G0xx_HAL_Driver/Inc/stm32g0xx_hal_adc.h             | C++          |        521 |      1,248 |        175 |      1,944 |
| /Users/bradr/Uni/FYP/Hybrid25_ECU/Code/ECU Servo/Drivers/STM32G0xx_HAL_Driver/Inc/stm32g0xx_hal_adc_ex.h          | C++          |         40 |        111 |         36 |        187 |
| /Users/bradr/Uni/FYP/Hybrid25_ECU/Code/ECU Servo/Drivers/STM32G0xx_HAL_Driver/Inc/stm32g0xx_hal_cortex.h          | C++          |        164 |        171 |         53 |        388 |
| /Users/bradr/Uni/FYP/Hybrid25_ECU/Code/ECU Servo/Drivers/STM32G0xx_HAL_Driver/Inc/stm32g0xx_hal_def.h             | C++          |        108 |         78 |         30 |        216 |
| /Users/bradr/Uni/FYP/Hybrid25_ECU/Code/ECU Servo/Drivers/STM32G0xx_HAL_Driver/Inc/stm32g0xx_hal_dma.h             | C++          |        428 |        274 |        102 |        804 |
| /Users/bradr/Uni/FYP/Hybrid25_ECU/Code/ECU Servo/Drivers/STM32G0xx_HAL_Driver/Inc/stm32g0xx_hal_dma_ex.h          | C++          |        114 |        110 |         55 |        279 |
| /Users/bradr/Uni/FYP/Hybrid25_ECU/Code/ECU Servo/Drivers/STM32G0xx_HAL_Driver/Inc/stm32g0xx_hal_exti.h            | C++          |        201 |        142 |         45 |        388 |
| /Users/bradr/Uni/FYP/Hybrid25_ECU/Code/ECU Servo/Drivers/STM32G0xx_HAL_Driver/Inc/stm32g0xx_hal_fdcan.h           | C++          |        622 |        634 |        187 |      1,443 |
| /Users/bradr/Uni/FYP/Hybrid25_ECU/Code/ECU Servo/Drivers/STM32G0xx_HAL_Driver/Inc/stm32g0xx_hal_flash.h           | C++          |        446 |        490 |         98 |      1,034 |
| /Users/bradr/Uni/FYP/Hybrid25_ECU/Code/ECU Servo/Drivers/STM32G0xx_HAL_Driver/Inc/stm32g0xx_hal_flash_ex.h        | C++          |         27 |         72 |         18 |        117 |
| /Users/bradr/Uni/FYP/Hybrid25_ECU/Code/ECU Servo/Drivers/STM32G0xx_HAL_Driver/Inc/stm32g0xx_hal_gpio.h            | C++          |        124 |        188 |         51 |        363 |
| /Users/bradr/Uni/FYP/Hybrid25_ECU/Code/ECU Servo/Drivers/STM32G0xx_HAL_Driver/Inc/stm32g0xx_hal_gpio_ex.h         | C++          |        457 |        274 |        106 |        837 |
| /Users/bradr/Uni/FYP/Hybrid25_ECU/Code/ECU Servo/Drivers/STM32G0xx_HAL_Driver/Inc/stm32g0xx_hal_i2c.h             | C++          |        326 |        396 |        117 |        839 |
| /Users/bradr/Uni/FYP/Hybrid25_ECU/Code/ECU Servo/Drivers/STM32G0xx_HAL_Driver/Inc/stm32g0xx_hal_i2c_ex.h          | C++          |         45 |        106 |         27 |        178 |
| /Users/bradr/Uni/FYP/Hybrid25_ECU/Code/ECU Servo/Drivers/STM32G0xx_HAL_Driver/Inc/stm32g0xx_hal_pcd.h             | C++          |        244 |        283 |        103 |        630 |
| /Users/bradr/Uni/FYP/Hybrid25_ECU/Code/ECU Servo/Drivers/STM32G0xx_HAL_Driver/Inc/stm32g0xx_hal_pcd_ex.h          | C++          |         21 |         47 |         21 |         89 |
| /Users/bradr/Uni/FYP/Hybrid25_ECU/Code/ECU Servo/Drivers/STM32G0xx_HAL_Driver/Inc/stm32g0xx_hal_pwr.h             | C++          |        100 |        186 |         40 |        326 |
| /Users/bradr/Uni/FYP/Hybrid25_ECU/Code/ECU Servo/Drivers/STM32G0xx_HAL_Driver/Inc/stm32g0xx_hal_pwr_ex.h          | C++          |        251 |        315 |         76 |        642 |
| /Users/bradr/Uni/FYP/Hybrid25_ECU/Code/ECU Servo/Drivers/STM32G0xx_HAL_Driver/Inc/stm32g0xx_hal_rcc.h             | C++          |      1,882 |        997 |        291 |      3,170 |
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

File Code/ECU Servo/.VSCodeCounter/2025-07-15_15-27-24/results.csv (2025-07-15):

filename | "language" | "C" | "C++" | "CMake Cache" | "JSON" | "LinkerScript" | "Assembly" | "CMake" | "YAML" | "comment" | "blank" | "total"
/Users/bradr/Uni/FYP/Hybrid25_ECU/Code/ECU Servo/CMakeCache.txt | "CMake Cache" | 0 | 0 | 329 | 0 | 0 | 0 | 0 | 0 | 0 | 73 | 402
/Users/bradr/Uni/FYP/Hybrid25_ECU/Code/ECU Servo/CMakeFiles/4.0.1/CMakeASMCompiler.cmake | "CMake" | 0 | 0 | 0 | 0 | 0 | 0 | 24 | 0 | 0 | 7 | 31
/Users/bradr/Uni/FYP/Hybrid25_ECU/Code/ECU Servo/CMakeFiles/4.0.1/CMakeCCompiler.cmake | "CMake" | 0 | 0 | 0 | 0 | 0 | 0 | 66 | 0 | 0 | 18 | 84
/Users/bradr/Uni/FYP/Hybrid25_ECU/Code/ECU Servo/CMakeFiles/4.0.1/CMakeCXXCompiler.cmake | "CMake" | 0 | 0 | 0 | 0 | 0 | 0 | 82 | 0 | 0 | 26 | 108
/Users/bradr/Uni/FYP/Hybrid25_ECU/Code/ECU Servo/CMakeFiles/4.0.1/CMakeSystem.cmake | "CMake" | 0 | 0 | 0 | 0 | 0 | 0 | 10 | 0 | 0 | 6 | 16
/Users/bradr/Uni/FYP/Hybrid25_ECU/Code/ECU Servo/CMakeFiles/4.0.1/CompilerIdC/CMakeCCompilerId.c | "C" | 690 | 0 | 0 | 0 | 0 | 0 | 0 | 0 | 61 | 155 | 906
/Users/bradr/Uni/FYP/Hybrid25_ECU/Code/ECU Servo/CMakeFiles/4.0.1/CompilerIdCXX/CMakeCXXCompilerId.cpp | "C++" | 0 | 708 | 0 | 0 | 0 | 0 | 0 | 0 | 62 | 151 | 921
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

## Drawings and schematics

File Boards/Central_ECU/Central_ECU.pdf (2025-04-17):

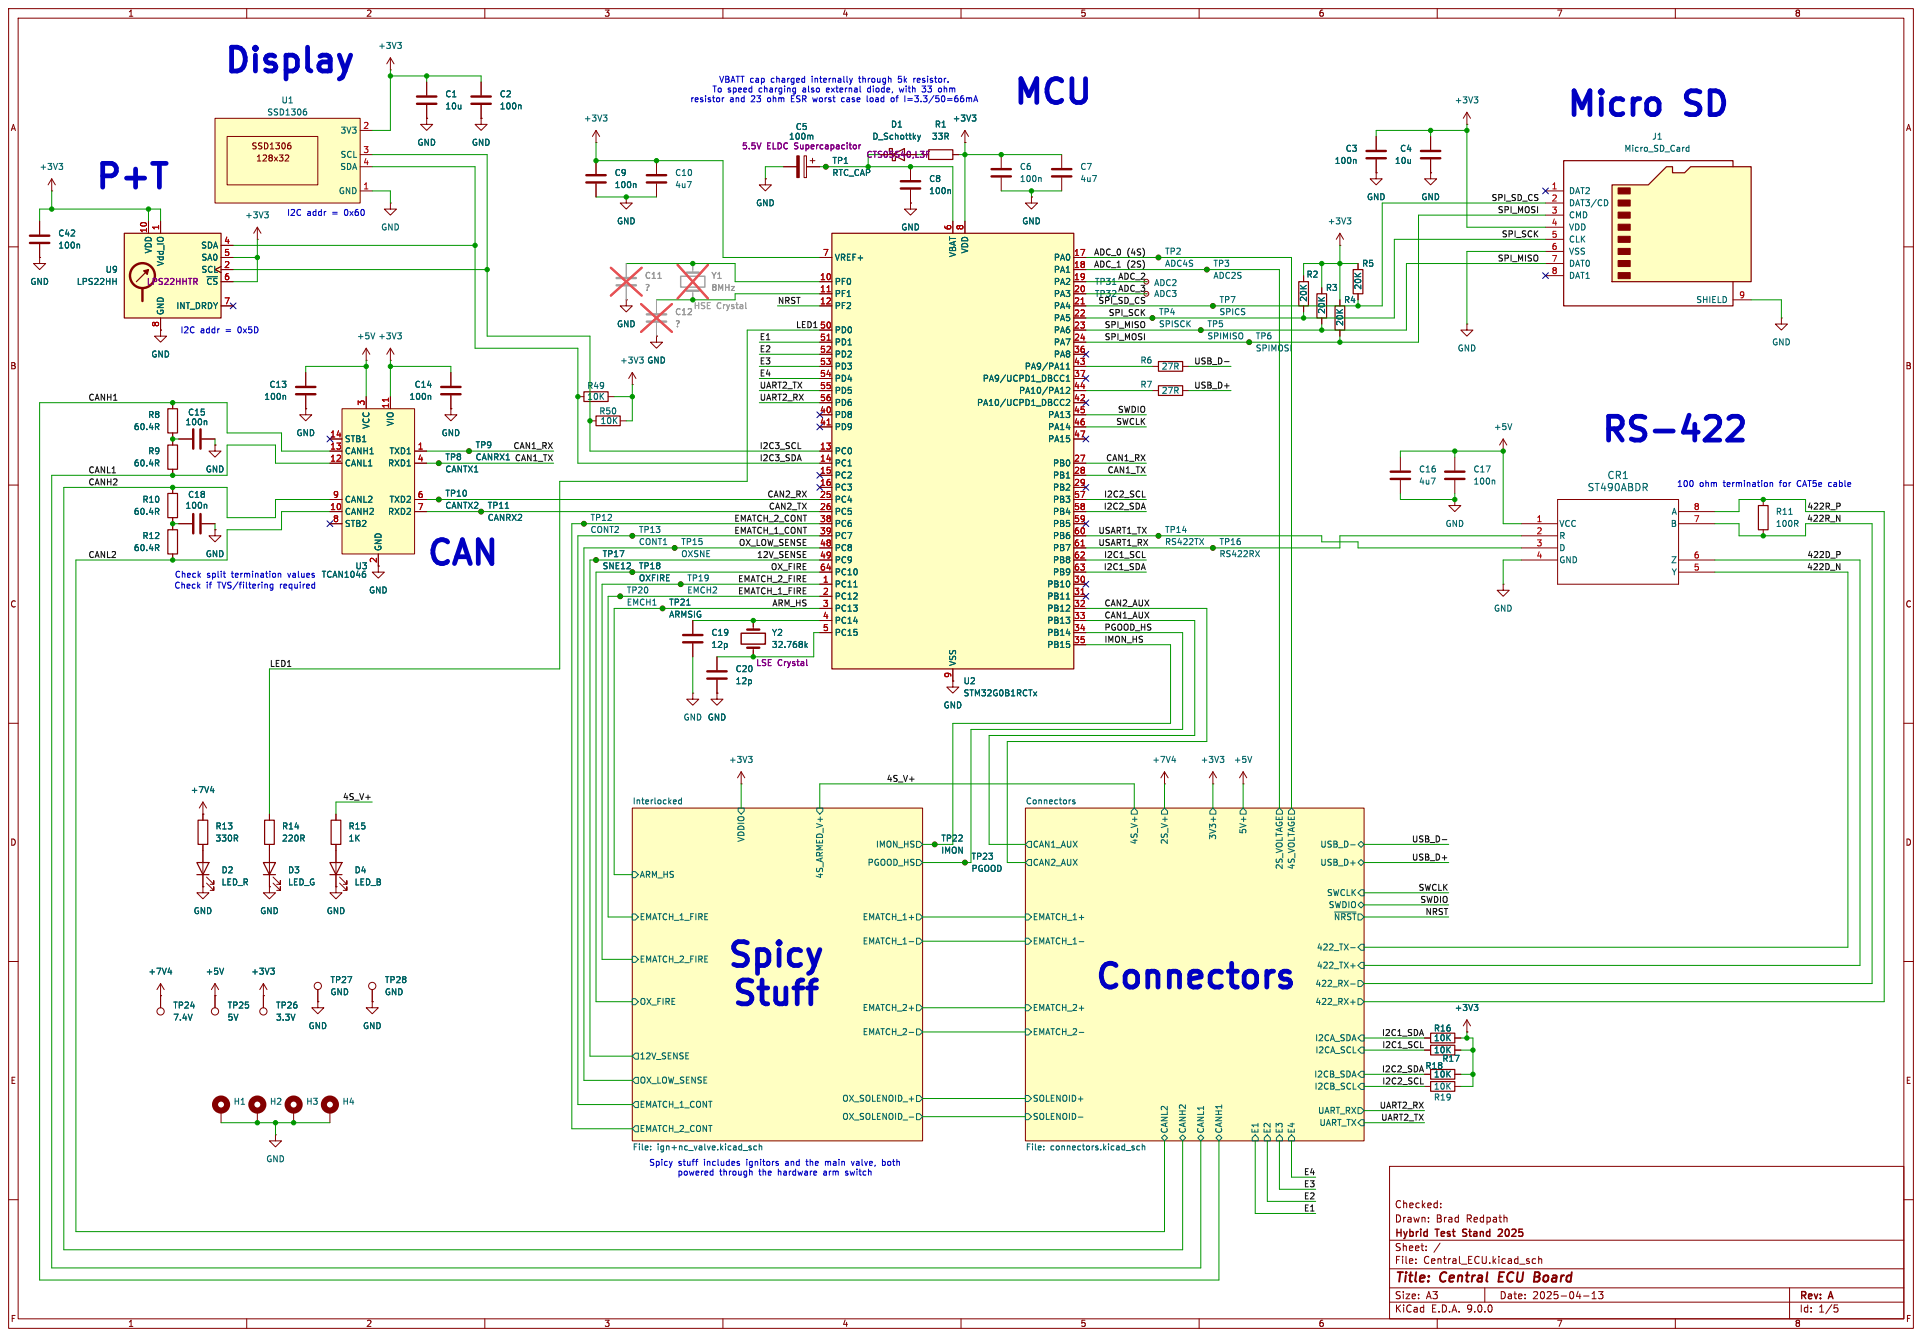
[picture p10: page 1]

powered through the hardware arm switch

Id: 1/5 Title: Central ECU Board

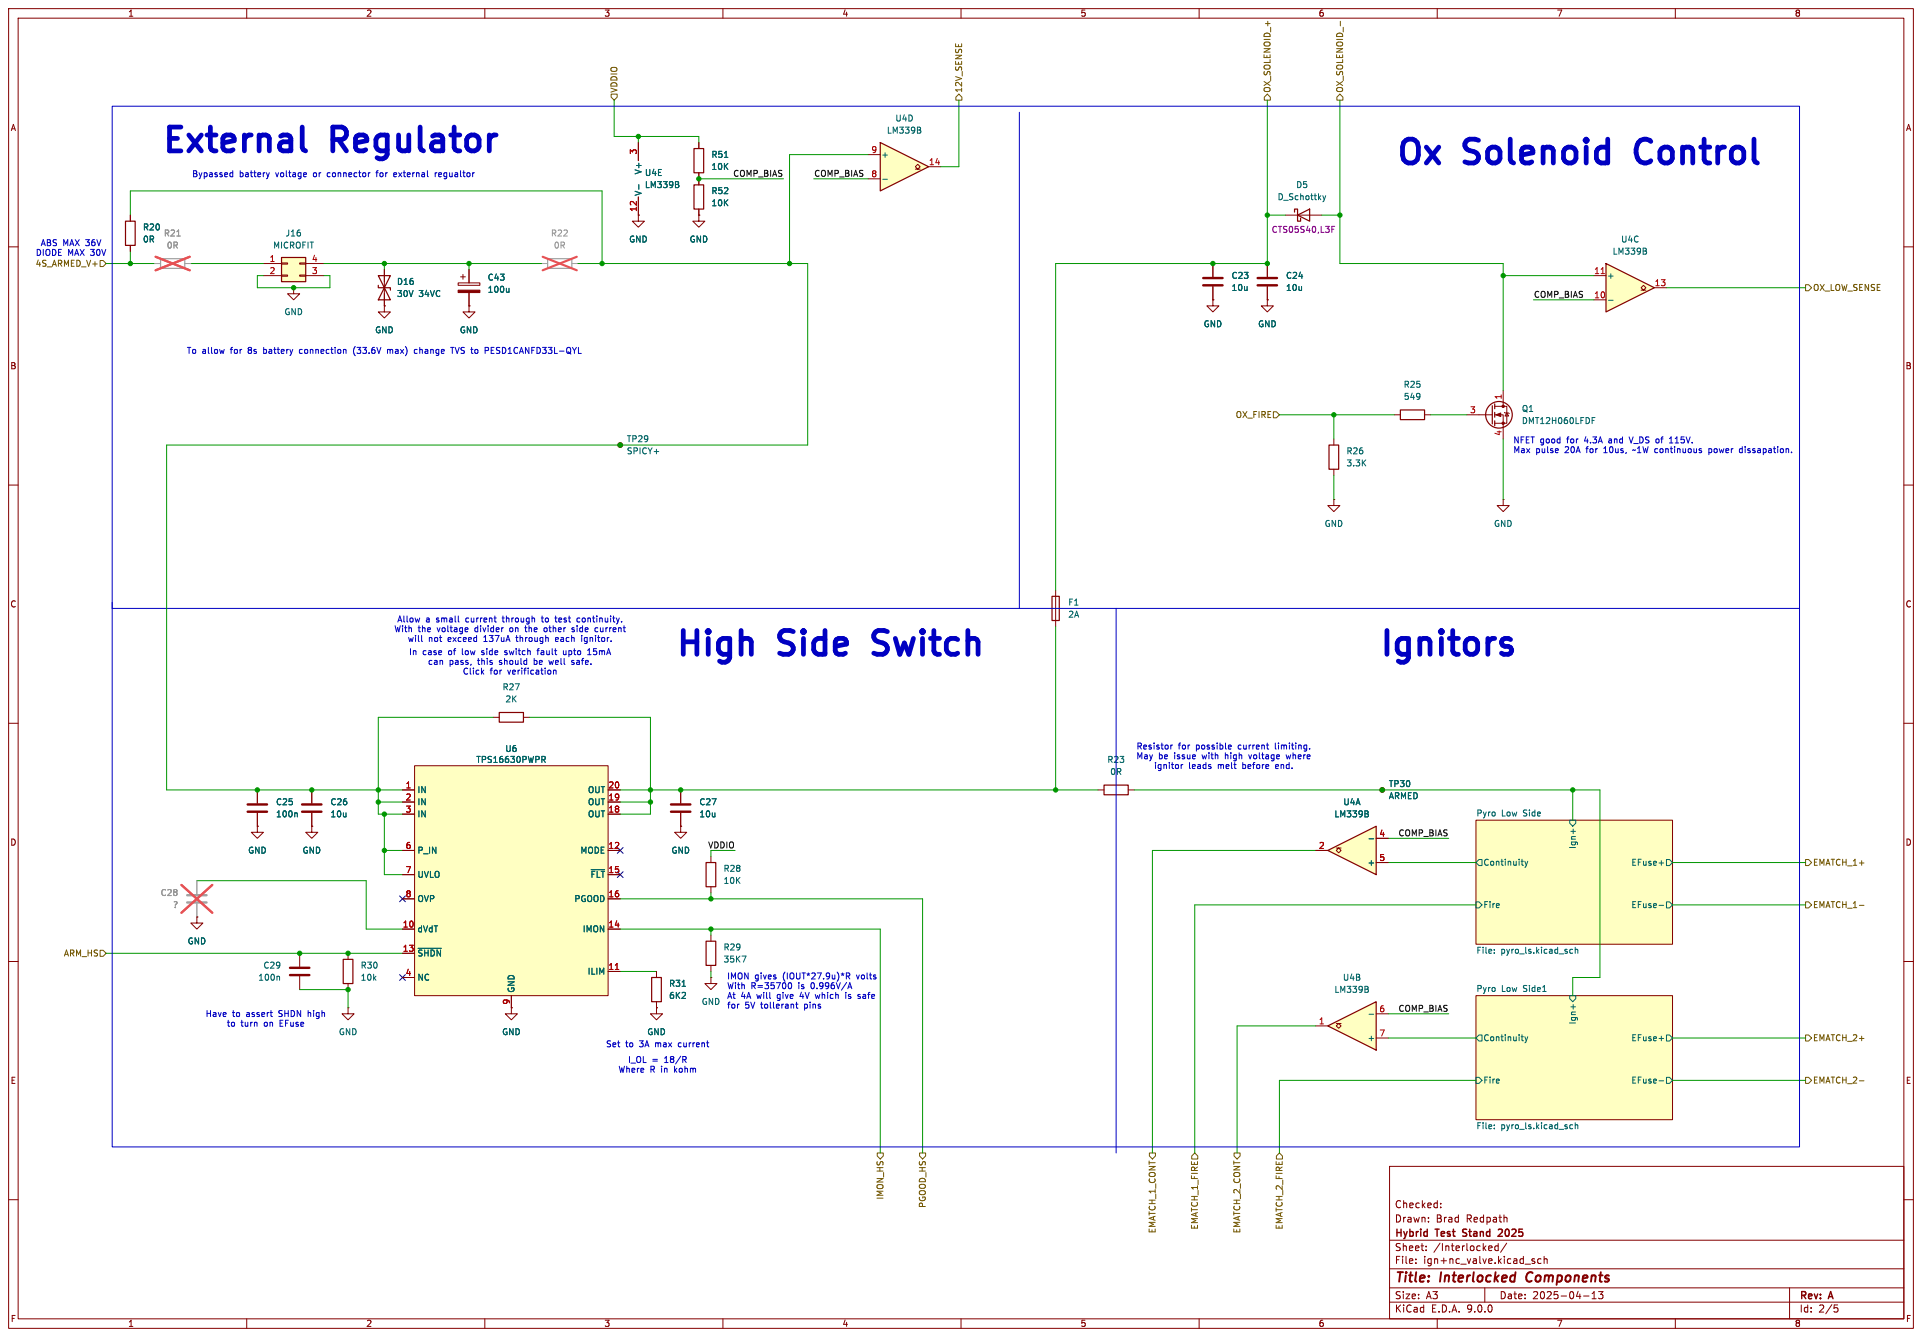
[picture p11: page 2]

can pass, this should be well safe. Click for verification (https://tinyurl.com/2eccyyuz) Allow a small current through to test continuity. With the voltage divider on the other side current will not exceed 137uA through each ignitor. Have to assert SHDN high

In case of low side switch fault upto 15mA

May be issue with high voltage where

9 OUT 20 OUT 19 OUT 18 MODE 12 ~{FLT} 15 PGOOD 16

Pyro Low Side File: pyro_ls.kicad_sch R30

At 4A will give 4V which is safe

to turn on EFuse

Id: 2/5 Title: Interlocked Components

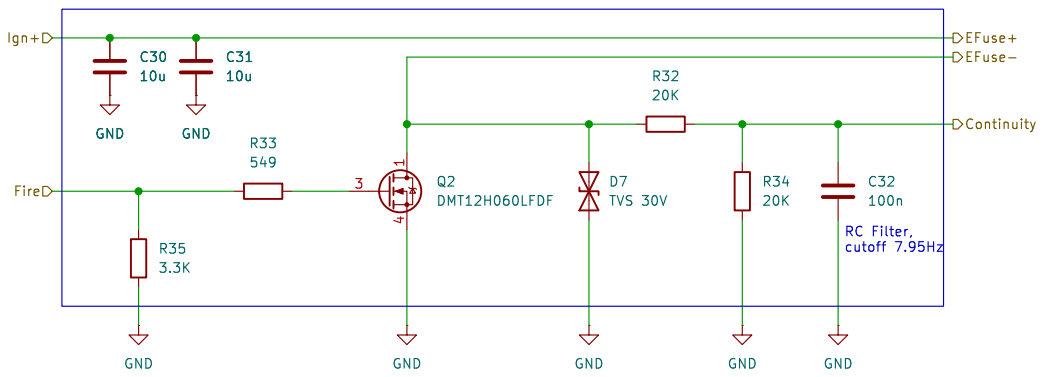
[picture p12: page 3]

Continuity RC Filter, cutoff 7.95Hz C31
10u GND

Id: 3/5 Title: Pyro Low Side

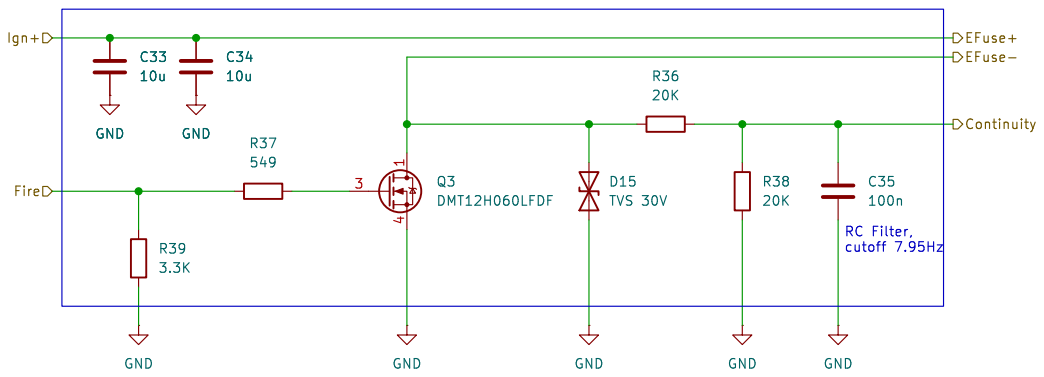
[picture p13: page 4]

Continuity RC Filter, cutoff 7.95Hz C34
10u GND

Id: 4/5 Title: Pyro Low Side

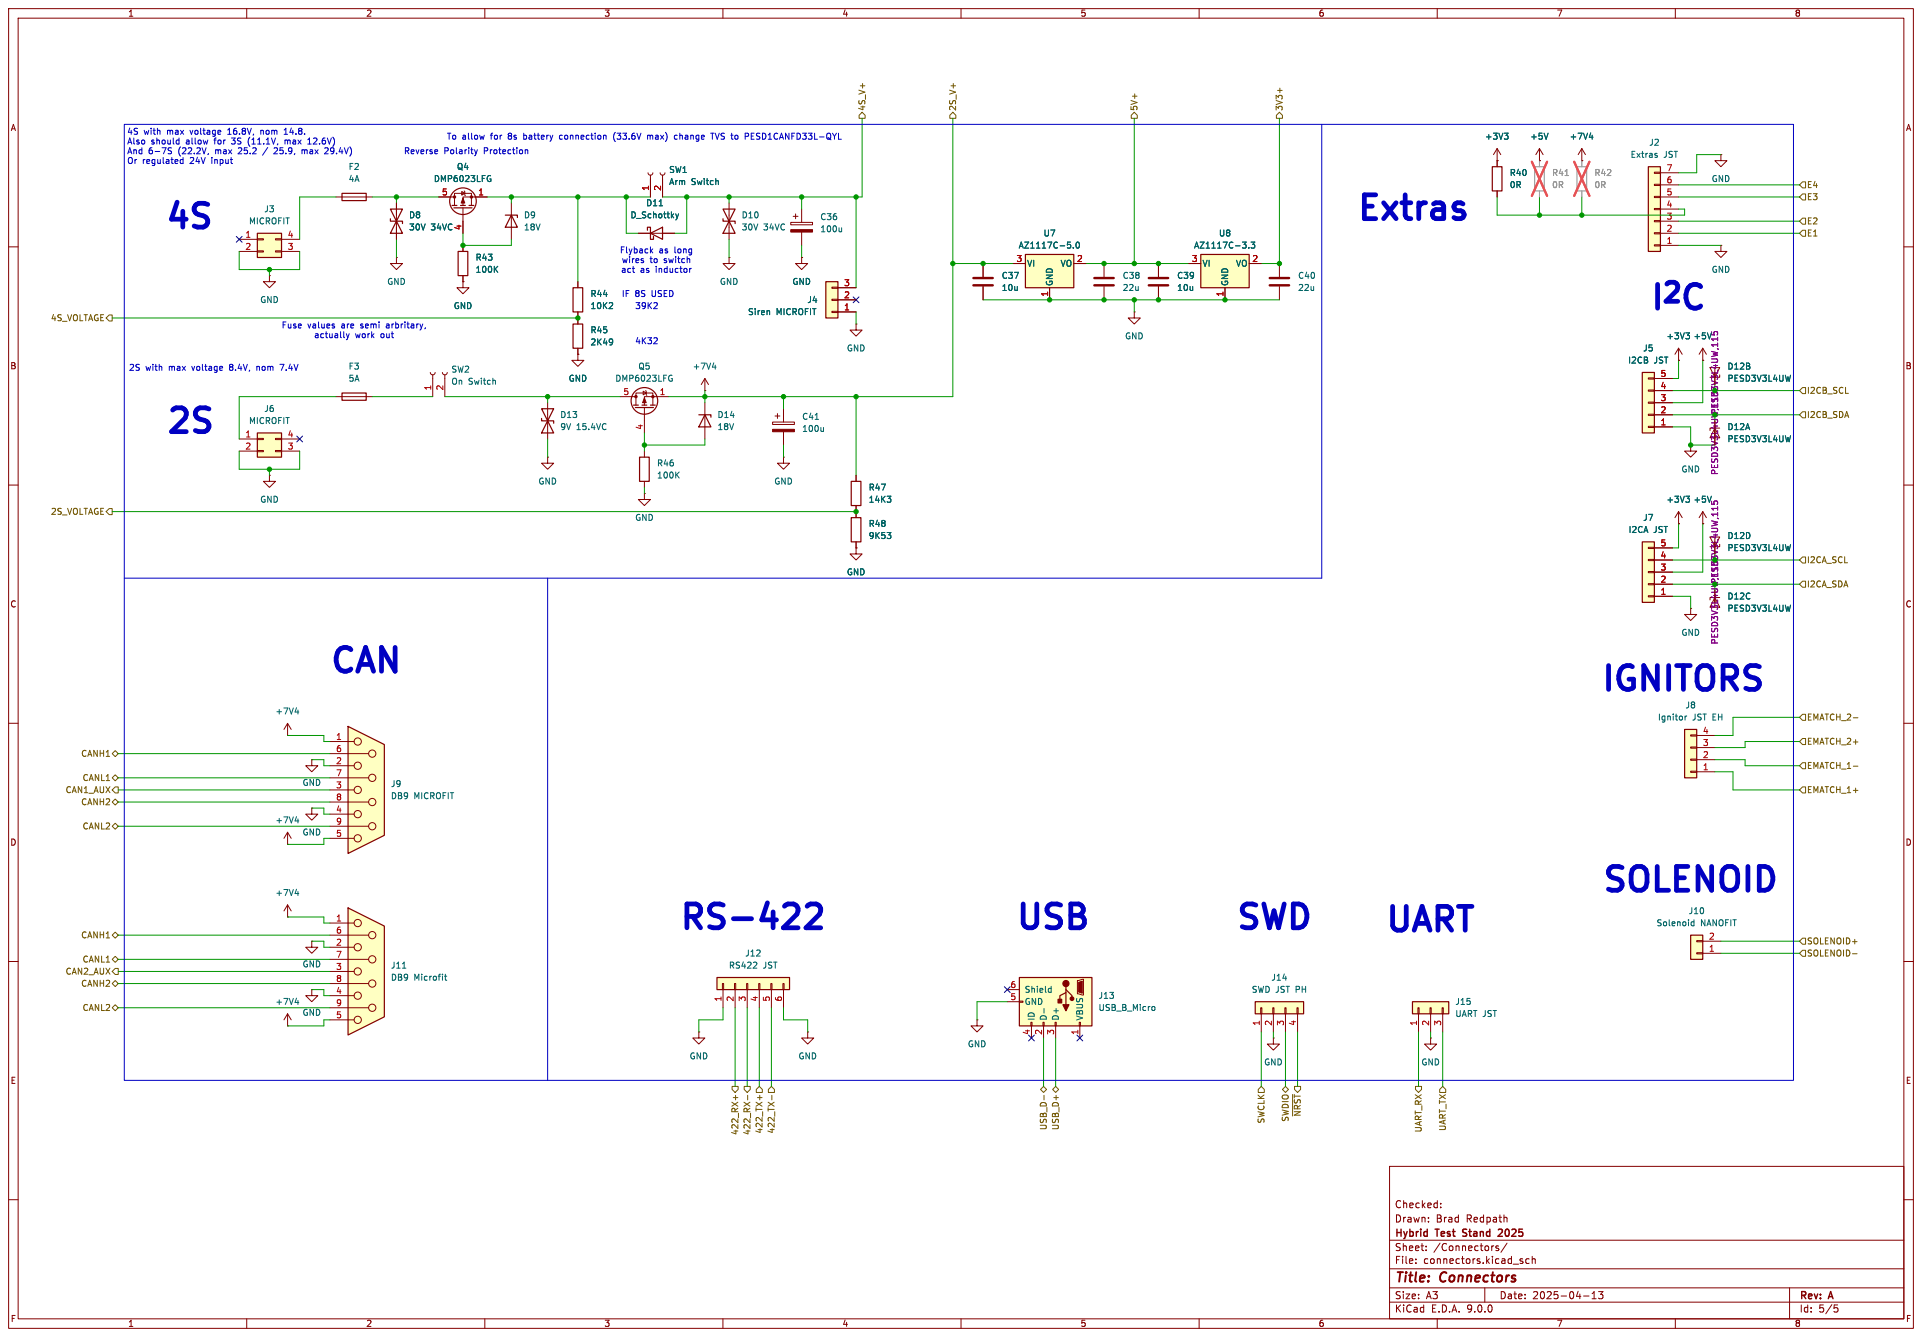
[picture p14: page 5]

Fuse values are semi arbritary,

2S with max voltage 8.4V, nom 7.4V

J14 SWD JST PH GND

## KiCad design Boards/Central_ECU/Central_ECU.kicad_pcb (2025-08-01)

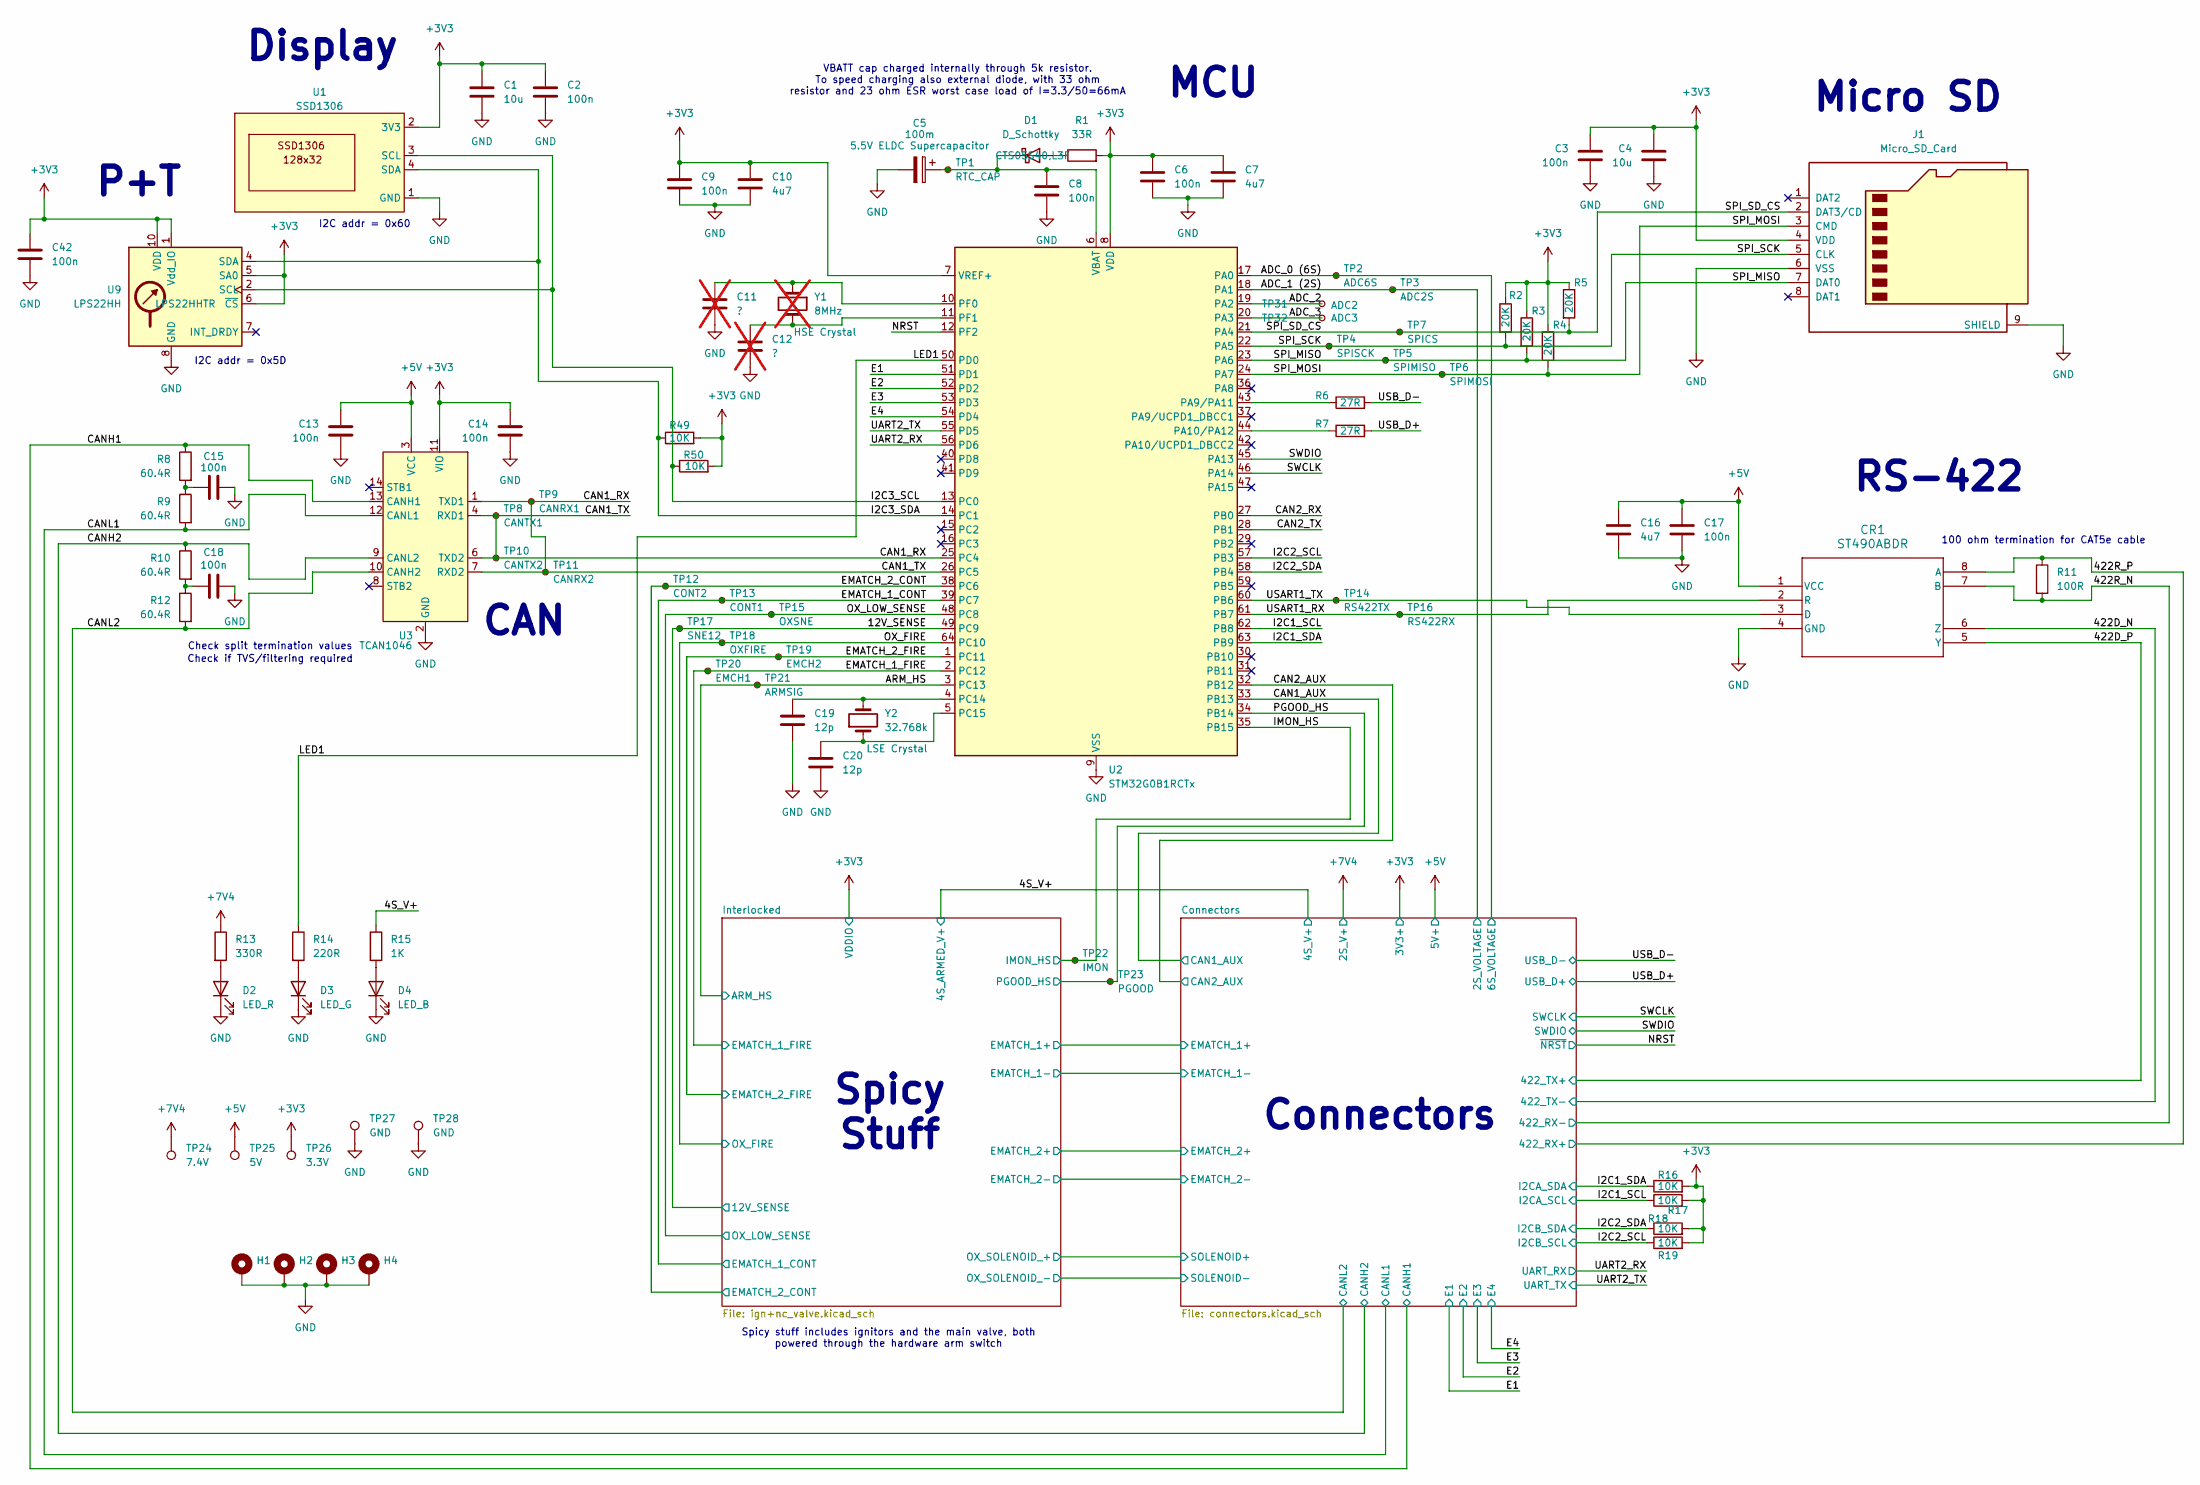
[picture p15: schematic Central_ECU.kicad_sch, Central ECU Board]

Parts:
C1, C4: 10u; C_0603_1608Metric
C2, C3, C13, C14, C15, C17, C18, C42: 100n; C_0603_1608Metric
C5: 100m; CP_Radial_D14.0mm_P5.00mm; MPN RSCBN1045R5G07014T
C6, C8, C9: 100n; C_0402_1005Metric
C7, C10, C16: 4u7; C_0603_1608Metric
C11, C12: ?; C_0402_1005Metric; not fitted
C19, C20: 12p; C_0402_1005Metric
CR1: ST490ABDR; SO-8_3.9x4.9mm_P1.27mm; MPN ST490ABDR
D1: D_Schottky; D_SOD-882; MPN CTS05S40,L3F
D2: LED_R; LED_1206_3216Metric; MPN LTST-C150KRKT
D3: LED_G; LED_1206_3216Metric; MPN LTST-C150KGKT
D4: LED_B; LED_1206_3216Metric; MPN LTST-C150TBKT
H1, H2, H3, H4: MountingHole_3.2mm_M3_DIN965_Pad_TopOnly
J1: Micro_SD_Card; microSD_HC_Molex_47219-2001; MPN 0472192001
R1: 33R; R_0603_1608Metric
R2, R3, R4, R5: 20K; R_0603_1608Metric
R6, R7: 27R; R_0603_1608Metric
R8, R9, R10, R12: 60.4R; R_0603_1608Metric
R11: 100R; R_0603_1608Metric
R13: 330R; R_0603_1608Metric
R14: 220R; R_0603_1608Metric
R15: 1K; R_0603_1608Metric
R16, R17, R18, R19, R49, R50: 10K; R_0603_1608Metric
TP1: RTC_CAP; TestPoint_Pad_1.5x1.5mm
TP2: ADC6S; TestPoint_Pad_1.5x1.5mm
TP3: ADC2S; TestPoint_Pad_1.5x1.5mm
TP4: SPISCK; TestPoint_Pad_1.5x1.5mm
TP5: SPIMISO; TestPoint_Pad_1.5x1.5mm
TP6: SPIMOSI; TestPoint_Pad_1.5x1.5mm
TP7: SPICS; TestPoint_Pad_1.5x1.5mm
TP8: CANTX1; TestPoint_Pad_1.5x1.5mm
TP9: CANRX1; TestPoint_Pad_1.5x1.5mm
TP10: CANTX2; TestPoint_Pad_1.5x1.5mm
TP11: CANRX2; TestPoint_Pad_1.5x1.5mm
TP12: CONT2; TestPoint_Pad_1.5x1.5mm
TP13: CONT1; TestPoint_Pad_1.5x1.5mm
TP14: RS422TX; TestPoint_Pad_1.5x1.5mm
TP15: OXSNE; TestPoint_Pad_1.5x1.5mm
TP16: RS422RX; TestPoint_Pad_1.5x1.5mm
TP17: SNE12; TestPoint_Pad_1.5x1.5mm
TP18: OXFIRE; TestPoint_Pad_1.5x1.5mm
TP19: EMCH2; TestPoint_Pad_1.5x1.5mm
TP20: EMCH1; TestPoint_Pad_1.5x1.5mm
TP21: ARMSIG; TestPoint_Pad_1.5x1.5mm
TP22: IMON; TestPoint_Pad_1.5x1.5mm
TP23: PGOOD; TestPoint_Pad_1.5x1.5mm
TP24: 7.4V; TestPoint_Pad_1.5x1.5mm
TP25: 5V; TestPoint_Pad_1.5x1.5mm
TP26: 3.3V; TestPoint_Pad_1.5x1.5mm
TP27, TP28: GND; TestPoint_Bridge_Pitch2.54mm_Drill1.3mm
TP31: ADC2; TestPoint_Pad_1.5x1.5mm
TP32: ADC3; TestPoint_Pad_1.5x1.5mm
U1: SSD1306; SSD1306-0.91-OLED-4pin-128x32; MPN N/A
U2: STM32G0B1RCTx; LQFP-64_10x10mm_P0.5mm; MPN STM32G0B1RCT6
U3: TCAN1046; SOT23_DYY_TEX; MPN TCAN1046AVDYYRQ1
U9: LPS22HH; ST_HLGA-10_2x2mm_P0.5mm_LayoutBorder3x2y; MPN LPS22HHTR
Y1: 8MHz; Crystal_SMD_Abracon_ABM8G-4Pin_3.2x2.5mm; not fitted
Y2: 32.768k; Crystal_SMD_2012-2Pin_2.0x1.2mm; MPN ABS06-32.768KHZ-1-T

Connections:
+3V3: C1.1, C2.1, C3.1, C4.1, C6.1, C7.1, C9.1, C10.1, C14.1, C42.1, J1.4 (VDD), R1.2, R2.1, R3.1, R4.1, R5.1, R16.2, R17.2, R18.2, R19.2, R49.2, R50.2, TP26.1, U1.2 (3V3), U2.7 (VREF+), U2.8 (VDD), U3.11 (VIO), U9.1 (Vdd_IO), U9.5 (SA0), U9.6 (~CS), U9.10 (VDD); also elsewhere on the board
+5V: C13.1, C16.1, C17.1, CR1.1 (VCC), TP25.1, U3.3 (VCC); also elsewhere on the board
+7V4: R13.1, TP24.1; also elsewhere on the board
/4S_V+: R15.1; also elsewhere on the board
/12V_SENSE: TP17.1, U2.49 (PC9); also elsewhere on the board
/422D_N: CR1.6 (Z); also elsewhere on the board
/422D_P: CR1.5 (Y); also elsewhere on the board
/422R_N: CR1.7 (B), R11.2; also elsewhere on the board
/422R_P: CR1.8 (A), R11.1; also elsewhere on the board
/ADC_0 (6S): TP2.1, U2.17 (PA0); also elsewhere on the board
/ADC_1 (2S): TP3.1, U2.18 (PA1); also elsewhere on the board
/ADC_2: TP31.1, U2.19 (PA2)
/ADC_3: TP32.1, U2.20 (PA3)
/ARM_HS: TP21.1, U2.3 (PC13); also elsewhere on the board
/CAN1_AUX: U2.33 (PB13); also elsewhere on the board
/CAN1_RX: TP8.1, TP9.1, TP10.1, TP11.1, U2.25 (PC4), U2.26 (PC5), U3.1 (TXD1), U3.4 (RXD1), U3.6 (TXD2), U3.7 (RXD2)
/CAN2_AUX: U2.32 (PB12); also elsewhere on the board
/CAN2_RX: U2.27 (PB0)
/CAN2_TX: U2.28 (PB1)
/CANH1: R8.1, U3.13 (CANH1); also elsewhere on the board
/CANH2: R10.1, U3.9 (CANL2); also elsewhere on the board
/CANL1: R9.2, U3.12 (CANL1); also elsewhere on the board
/CANL2: R12.2, U3.10 (CANH2); also elsewhere on the board
/E1: U2.51 (PD1); also elsewhere on the board
/E2: U2.52 (PD2); also elsewhere on the board
/E3: U2.53 (PD3); also elsewhere on the board
/E4: U2.54 (PD4); also elsewhere on the board
/EMATCH_1_CONT: TP13.1, U2.39 (PC7); also elsewhere on the board
/EMATCH_1_FIRE: TP20.1, U2.2 (PC12); also elsewhere on the board
/EMATCH_2_CONT: TP12.1, U2.38 (PC6); also elsewhere on the board
/EMATCH_2_FIRE: TP19.1, U2.1 (PC11); also elsewhere on the board
/I2C1_SCL: R17.1, U2.62 (PB8); also elsewhere on the board
/I2C1_SDA: R16.1, U2.63 (PB9); also elsewhere on the board
/I2C2_SCL: R19.1, U2.57 (PB3); also elsewhere on the board
/I2C2_SDA: R18.1, U2.58 (PB4); also elsewhere on the board
/I2C3_SCL: R50.1, U1.3 (SCL), U2.13 (PC0), U9.2 (SCL)
/I2C3_SDA: R49.1, U1.4 (SDA), U2.14 (PC1), U9.4 (SDA)
/IMON_HS: TP22.1, U2.35 (PB15); also elsewhere on the board
/LED1: R14.1, U2.50 (PD0)
/NRST: U2.12 (PF2); also elsewhere on the board
/OX_FIRE: TP18.1, U2.64 (PC10); also elsewhere on the board
/OX_LOW_SENSE: TP15.1, U2.48 (PC8); also elsewhere on the board
/PGOOD_HS: TP23.1, U2.34 (PB14); also elsewhere on the board
/SPI_MISO: J1.7 (DAT0), R3.2, TP5.1, U2.23 (PA6)
/SPI_MOSI: J1.3 (CMD), R4.2, TP6.1, U2.24 (PA7)
/SPI_SCK: J1.5 (CLK), R2.2, TP4.1, U2.22 (PA5)
/SPI_SD_CS: J1.2 (DAT3/CD), R5.2, TP7.1, U2.21 (PA4)
/SWCLK: U2.46 (PA14); also elsewhere on the board
/SWDIO: U2.45 (PA13); also elsewhere on the board
/UART2_RX: U2.56 (PD6); also elsewhere on the board
/UART2_TX: U2.55 (PD5); also elsewhere on the board
/USART1_RX: CR1.2 (R), TP16.1, U2.61 (PB7)
/USART1_TX: CR1.3 (D), TP14.1, U2.60 (PB6)
/USB_D+: R7.2; also elsewhere on the board
/USB_D-: R6.2; also elsewhere on the board
GND: C1.2, C2.2, C3.2, C4.2, C5.2, C6.2, C7.2, C8.2, C9.2, C10.2, C11.2, C12.2, C13.2, C14.2, C15.1, C16.2, C17.2, C18.1, C19.2, C20.2, C42.2, CR1.4 (GND), D2.1 (K), D3.1 (K), D4.1 (K), H1.1, H2.1, H3.1, H4.1, J1.6 (VSS), J1.9 (SHIELD), TP27.1, TP28.1, U1.1 (GND), U2.9 (VSS), U3.2 (GND), U3.5 (GND), U9.3 (GND), U9.8 (GND), U9.9 (GND); also elsewhere on the board
unnamed: C15.2, R8.2, R9.1
unnamed: C18.2, R10.2, R12.1
unnamed: D1.2 (A), R1.1
unnamed: C5.1, C8.1, D1.1 (K), TP1.1, U2.6 (VBAT)
unnamed: D2.2 (A), R13.2
unnamed: D3.2 (A), R14.2
unnamed: D4.2 (A), R15.2
unnamed: R6.1, U2.43 (PA9/PA11)
unnamed: R7.1, U2.44 (PA10/PA12)
unnamed: C19.1, U2.4 (PC14), Y2.2
unnamed: C20.1, U2.5 (PC15), Y2.1
unnamed: C11.1, U2.10 (PF0), Y1.1
unnamed: C12.1, U2.11 (PF1), Y1.3 (2)

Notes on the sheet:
VBATT cap charged internally through 5k resistor. To speed charging also external diode, with 33 ohm resistor and 23 ohm ESR worst case load of I=3.3/50=66mA
Display
Connectors
RS-422
I2C addr = 0x60
Spicy Stuff
100 ohm termination for CAT5e cable
I2C addr = 0x5D
CAN
P+T
Check if TVS/filtering required
Micro SD
Check split termination values
Spicy stuff includes ignitors and the main valve, both powered through the hardware arm switch
MCU

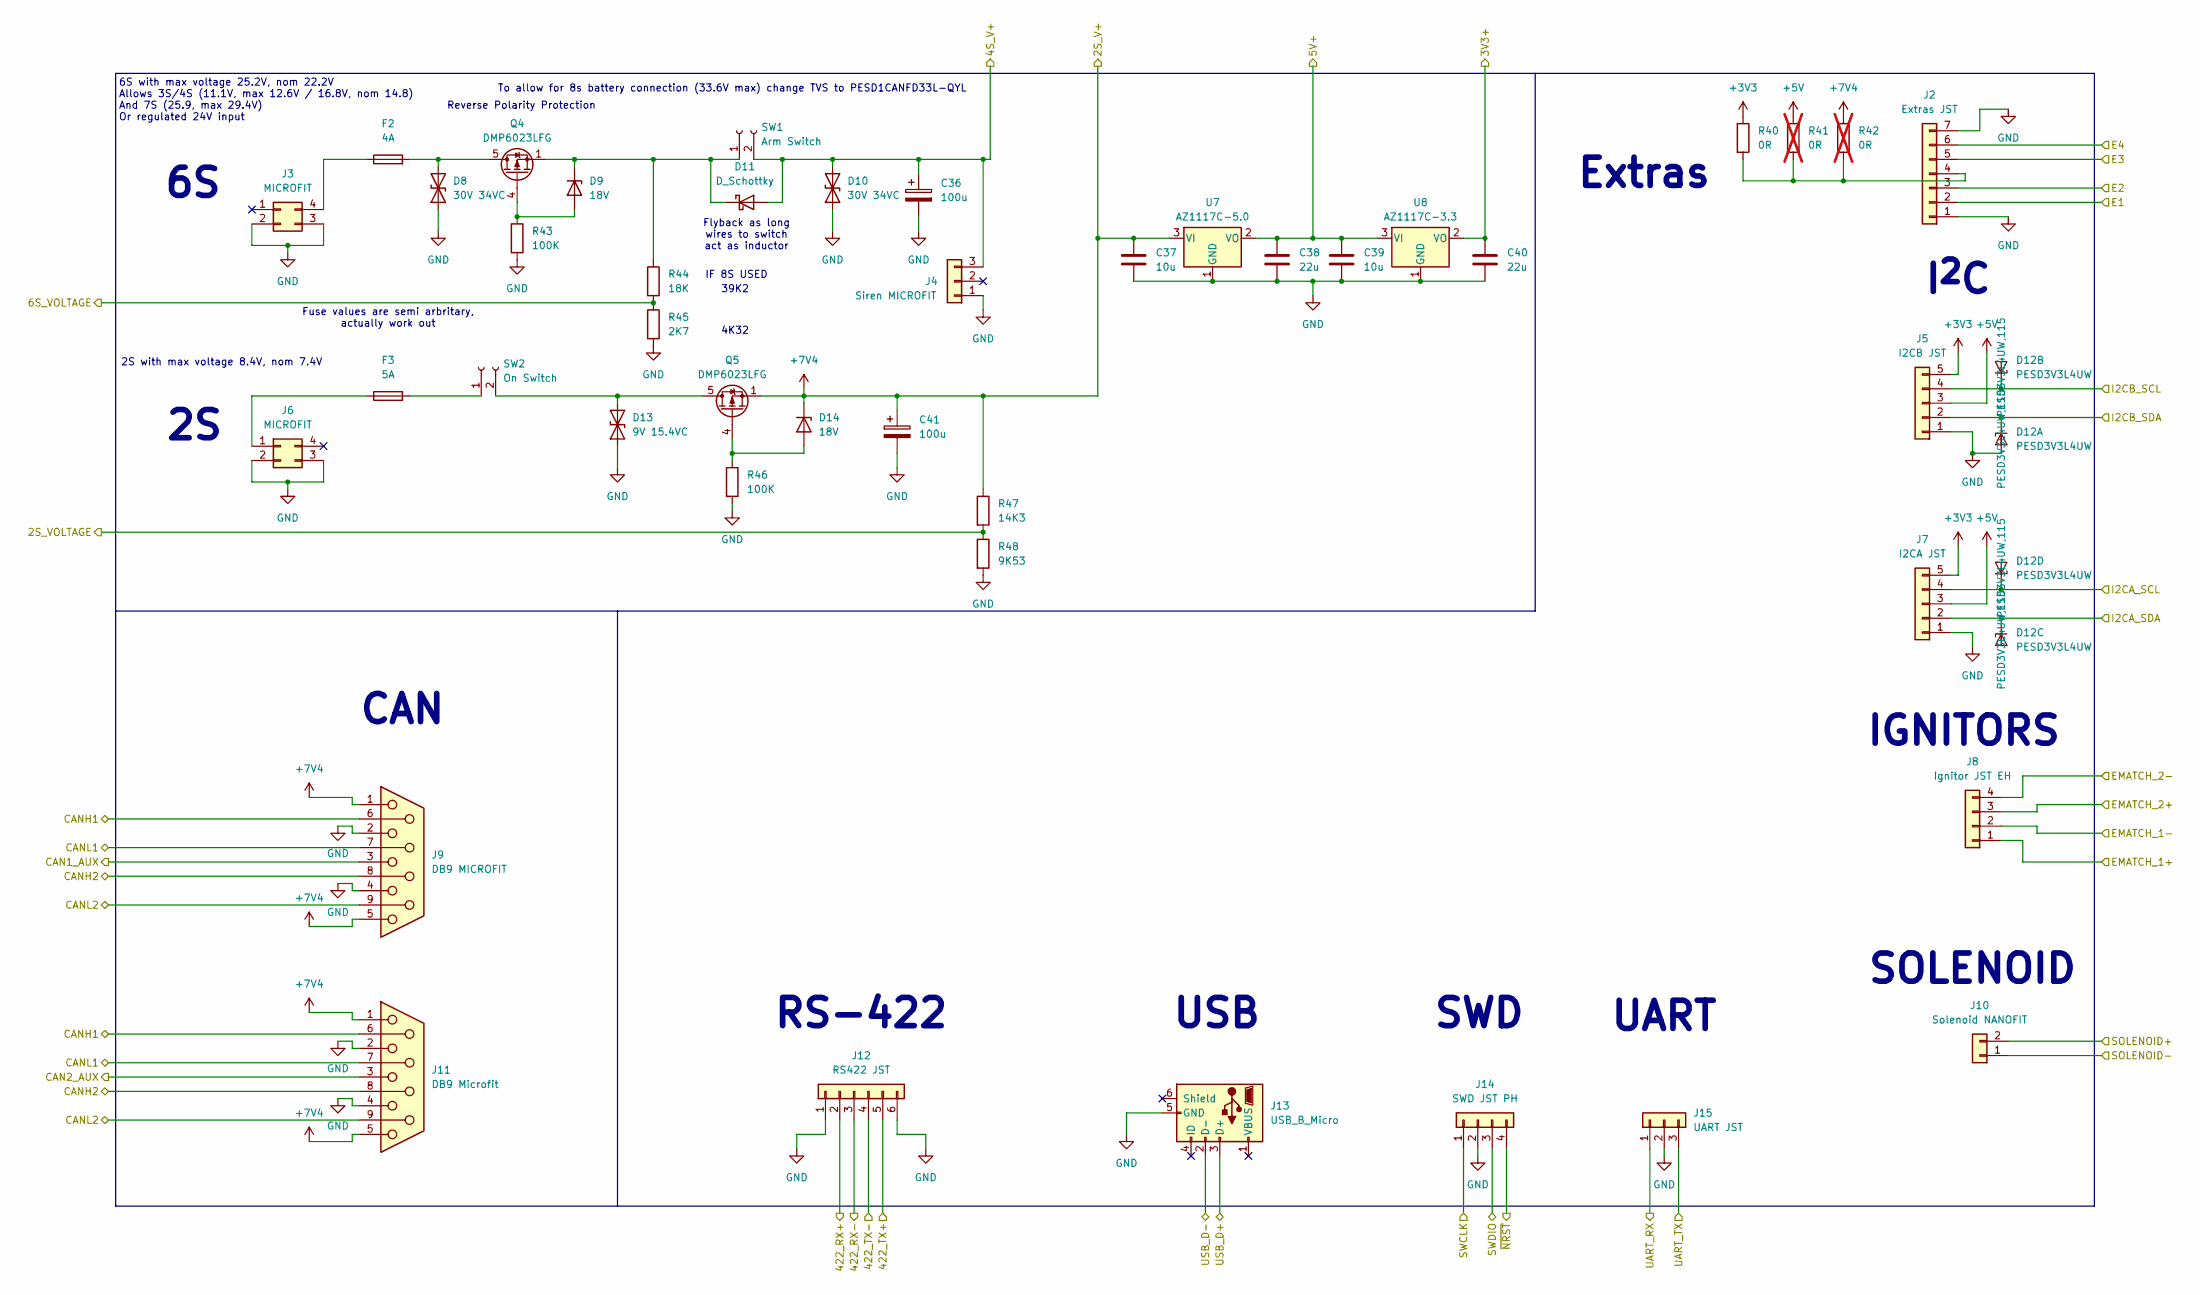
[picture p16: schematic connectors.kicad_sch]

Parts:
C36, C41: 100u; CP_Elec_8x10.5; MPN A768KS107M1HLAE030
C37, C39: 10u; C_0603_1608Metric
C38, C40: 22u; C_1206_3216Metric
D8, D10: 30V 34VC; D_SOD-882; MPN PESD1CANFD30L-QYL
D9, D14: 18V; D_SOD-323F; MPN MM3Z18VB
D11: D_Schottky; D_SOD-882; MPN CTS05S40,L3F
D12: PESD3V3L4UW; SOT-665; MPN PESD3V3L4UW,115
D13: 9V 15.4VC; D_SOD-123F; MPN SMF9.0CA
F2: 4A; Fuse_1206_3216Metric
F3: 5A; Fuse_1206_3216Metric
J2: Extras JST; JST_PH_B7B-PH-K_1x07_P2.00mm_Vertical; MPN B7B-PH-K-S
J3, J6: MICROFIT; Molex_Micro-Fit_3.0_43045-0412_2x02_P3.00mm_Vertical; MPN 0430450412
J4: Siren MICROFIT; Molex_Micro-Fit_3.0_43650-0315_1x03_P3.00mm_Vertical; MPN 436500315
J5: I2CB JST; JST_PH_B5B-PH-K_1x05_P2.00mm_Vertical; MPN B6B-PH-K-S
J7: I2CA JST; JST_PH_B5B-PH-K_1x05_P2.00mm_Vertical; MPN B5B-PH-K-S
J8: Ignitor JST EH; JST_EH_B4B-EH-A_1x04_P2.50mm_Vertical; MPN B4B-EH-A
J9: DB9 MICROFIT; Molex_Micro-Fit_3.0_43045-1012_2x05_P3.00mm_Vertical; MPN 0430451027
J10: Solenoid NANOFIT; Molex_Nano-Fit_105309-xx02_1x02_P2.50mm_Vertical; MPN 1053091102
J11: DB9 Microfit; Molex_Micro-Fit_3.0_43045-1012_2x05_P3.00mm_Vertical; MPN 0430451027
J12: RS422 JST; JST_PH_B6B-PH-K_1x06_P2.00mm_Vertical; MPN B6B-PH-K-S
J13: USB_B_Micro; USB_Micro-B_Amphenol_10118193-0001LF_Horizontal; MPN 10118193-0001LF
J14: SWD JST PH; JST_PH_B4B-PH-K_1x04_P2.00mm_Vertical; MPN B4B-PH-K-S
J15: UART JST; JST_PH_B3B-PH-K_1x03_P2.00mm_Vertical; MPN B3B-PH-K-S
Q4, Q5: DMP6023LFG; Diodes_PowerDI3333-8; MPN DMP6023LFG-7
R40: 0R; R_0603_1608Metric
R41, R42: 0R; R_0603_1608Metric; not fitted
R43, R46: 100K; R_0603_1608Metric
R44: 18K; R_0603_1608Metric
R45: 2K7; R_0603_1608Metric
R47: 14K3; R_0603_1608Metric
R48: 9K53; R_0603_1608Metric
SW1: Arm Switch; Molex_Micro-Fit_3.0_43650-0215_1x02_P3.00mm_Vertical; MPN 436500228
SW2: On Switch; Molex_Micro-Fit_3.0_43650-0215_1x02_P3.00mm_Vertical; MPN 436500228
U7: AZ1117C-5.0; SOT-223-3_TabPin2; MPN AZ1117CH-5.0TRG1
U8: AZ1117C-3.3; SOT-223-3_TabPin2; MPN AZ1117CH-3.3TRG1

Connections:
+3V3: C40.1, J5.5, J7.5, R40.1, U8.2 (VO); also elsewhere on the board
+5V: C38.1, C39.1, J5.3, J7.3, R41.1, U7.2 (VO), U8.3 (VI); also elsewhere on the board
+7V4: C37.1, C41.1, D14.1 (K), J9.1, J9.5, J11.1, J11.5, Q5.1 (S), Q5.2 (S), Q5.3 (S), R42.1, R47.1, U7.3 (VI); also elsewhere on the board
/4S_V+: C36.1, D10.2 (A2), D11.2 (A), J4.3, SW1.2; also elsewhere on the board
/422D_N: J12.4; also elsewhere on the board
/422D_P: J12.5; also elsewhere on the board
/422R_N: J12.3; also elsewhere on the board
/422R_P: J12.2; also elsewhere on the board
/ADC_0 (6S): R44.2, R45.1; also elsewhere on the board
/ADC_1 (2S): R47.2, R48.1; also elsewhere on the board
/CAN1_AUX: J9.3; also elsewhere on the board
/CAN2_AUX: J11.3; also elsewhere on the board
/CANH1: J9.6, J11.6; also elsewhere on the board
/CANH2: J9.8, J11.8; also elsewhere on the board
/CANL1: J9.7, J11.7; also elsewhere on the board
/CANL2: J9.9, J11.9; also elsewhere on the board
/Connectors/EMATCH_1+: J8.1, J8.3; also elsewhere on the board
/Connectors/EMATCH_1-: J8.2; also elsewhere on the board
/Connectors/EMATCH_2-: J8.4; also elsewhere on the board
/Connectors/SOLENOID+: J10.2; also elsewhere on the board
/Connectors/SOLENOID-: J10.1; also elsewhere on the board
/E1: J2.2; also elsewhere on the board
/E2: J2.3; also elsewhere on the board
/E3: J2.5; also elsewhere on the board
/E4: J2.6; also elsewhere on the board
/I2C1_SCL: D12.5 (K4), J7.4; also elsewhere on the board
/I2C1_SDA: D12.4 (K3), J7.2; also elsewhere on the board
/I2C2_SCL: D12.3 (K2), J5.4; also elsewhere on the board
/I2C2_SDA: D12.1 (K1), J5.2; also elsewhere on the board
/NRST: J14.4; also elsewhere on the board
/SWCLK: J14.1; also elsewhere on the board
/SWDIO: J14.3; also elsewhere on the board
/UART2_RX: J15.1; also elsewhere on the board
/UART2_TX: J15.3; also elsewhere on the board
/USB_D+: J13.3 (D+); also elsewhere on the board
/USB_D-: J13.2 (D-); also elsewhere on the board
GND: C36.2, C37.2, C38.2, C39.2, C40.2, C41.2, D8.1 (A1), D10.1 (A1), D12.2 (A), D13.1 (A1), J2.1, J2.7, J3.2, J3.3, J4.1, J5.1, J6.2, J6.3, J7.1, J9.2, J9.4, J11.2, J11.4, J12.1, J12.6, J13.5 (GND), J14.2, J15.2, R43.2, R45.2, R46.2, R48.2, U7.1 (GND), U8.1 (GND); also elsewhere on the board
unnamed: D8.2 (A2), F2.2, Q4.5 (D)
unnamed: D9.2 (A), Q4.4 (G), R43.1
unnamed: D9.1 (K), D11.1 (K), Q4.1 (S), Q4.2 (S), Q4.3 (S), R44.1, SW1.1
unnamed: D13.2 (A2), Q5.5 (D), SW2.2
unnamed: D14.2 (A), Q5.4 (G), R46.1
unnamed: J2.4, R40.2, R41.2, R42.2
unnamed: F2.1, J3.4
unnamed: F3.1, J6.1
unnamed: F3.2, SW2.1

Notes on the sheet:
CAN
To allow for 8s battery connection (33.6V max) change TVS to PESD1CANFD33L-QYL
USB
Flyback as long wires to switch act as inductor
SOLENOID
RS-422
IGNITORS
Extras
2S with max voltage 8.4V, nom 7.4V
Fuse values are semi arbritary, actually work out
4K32
6S with max voltage 25.2V, nom 22.2V Allows 3S/4S (11.1V, max 12.6V / 16.8V, nom 14.8) And 7S (25.9, max 29.4V) Or regulated 24V input
IF 8S USED
39K2
Reverse Polarity Protection
UART
SWD
I^{2}C

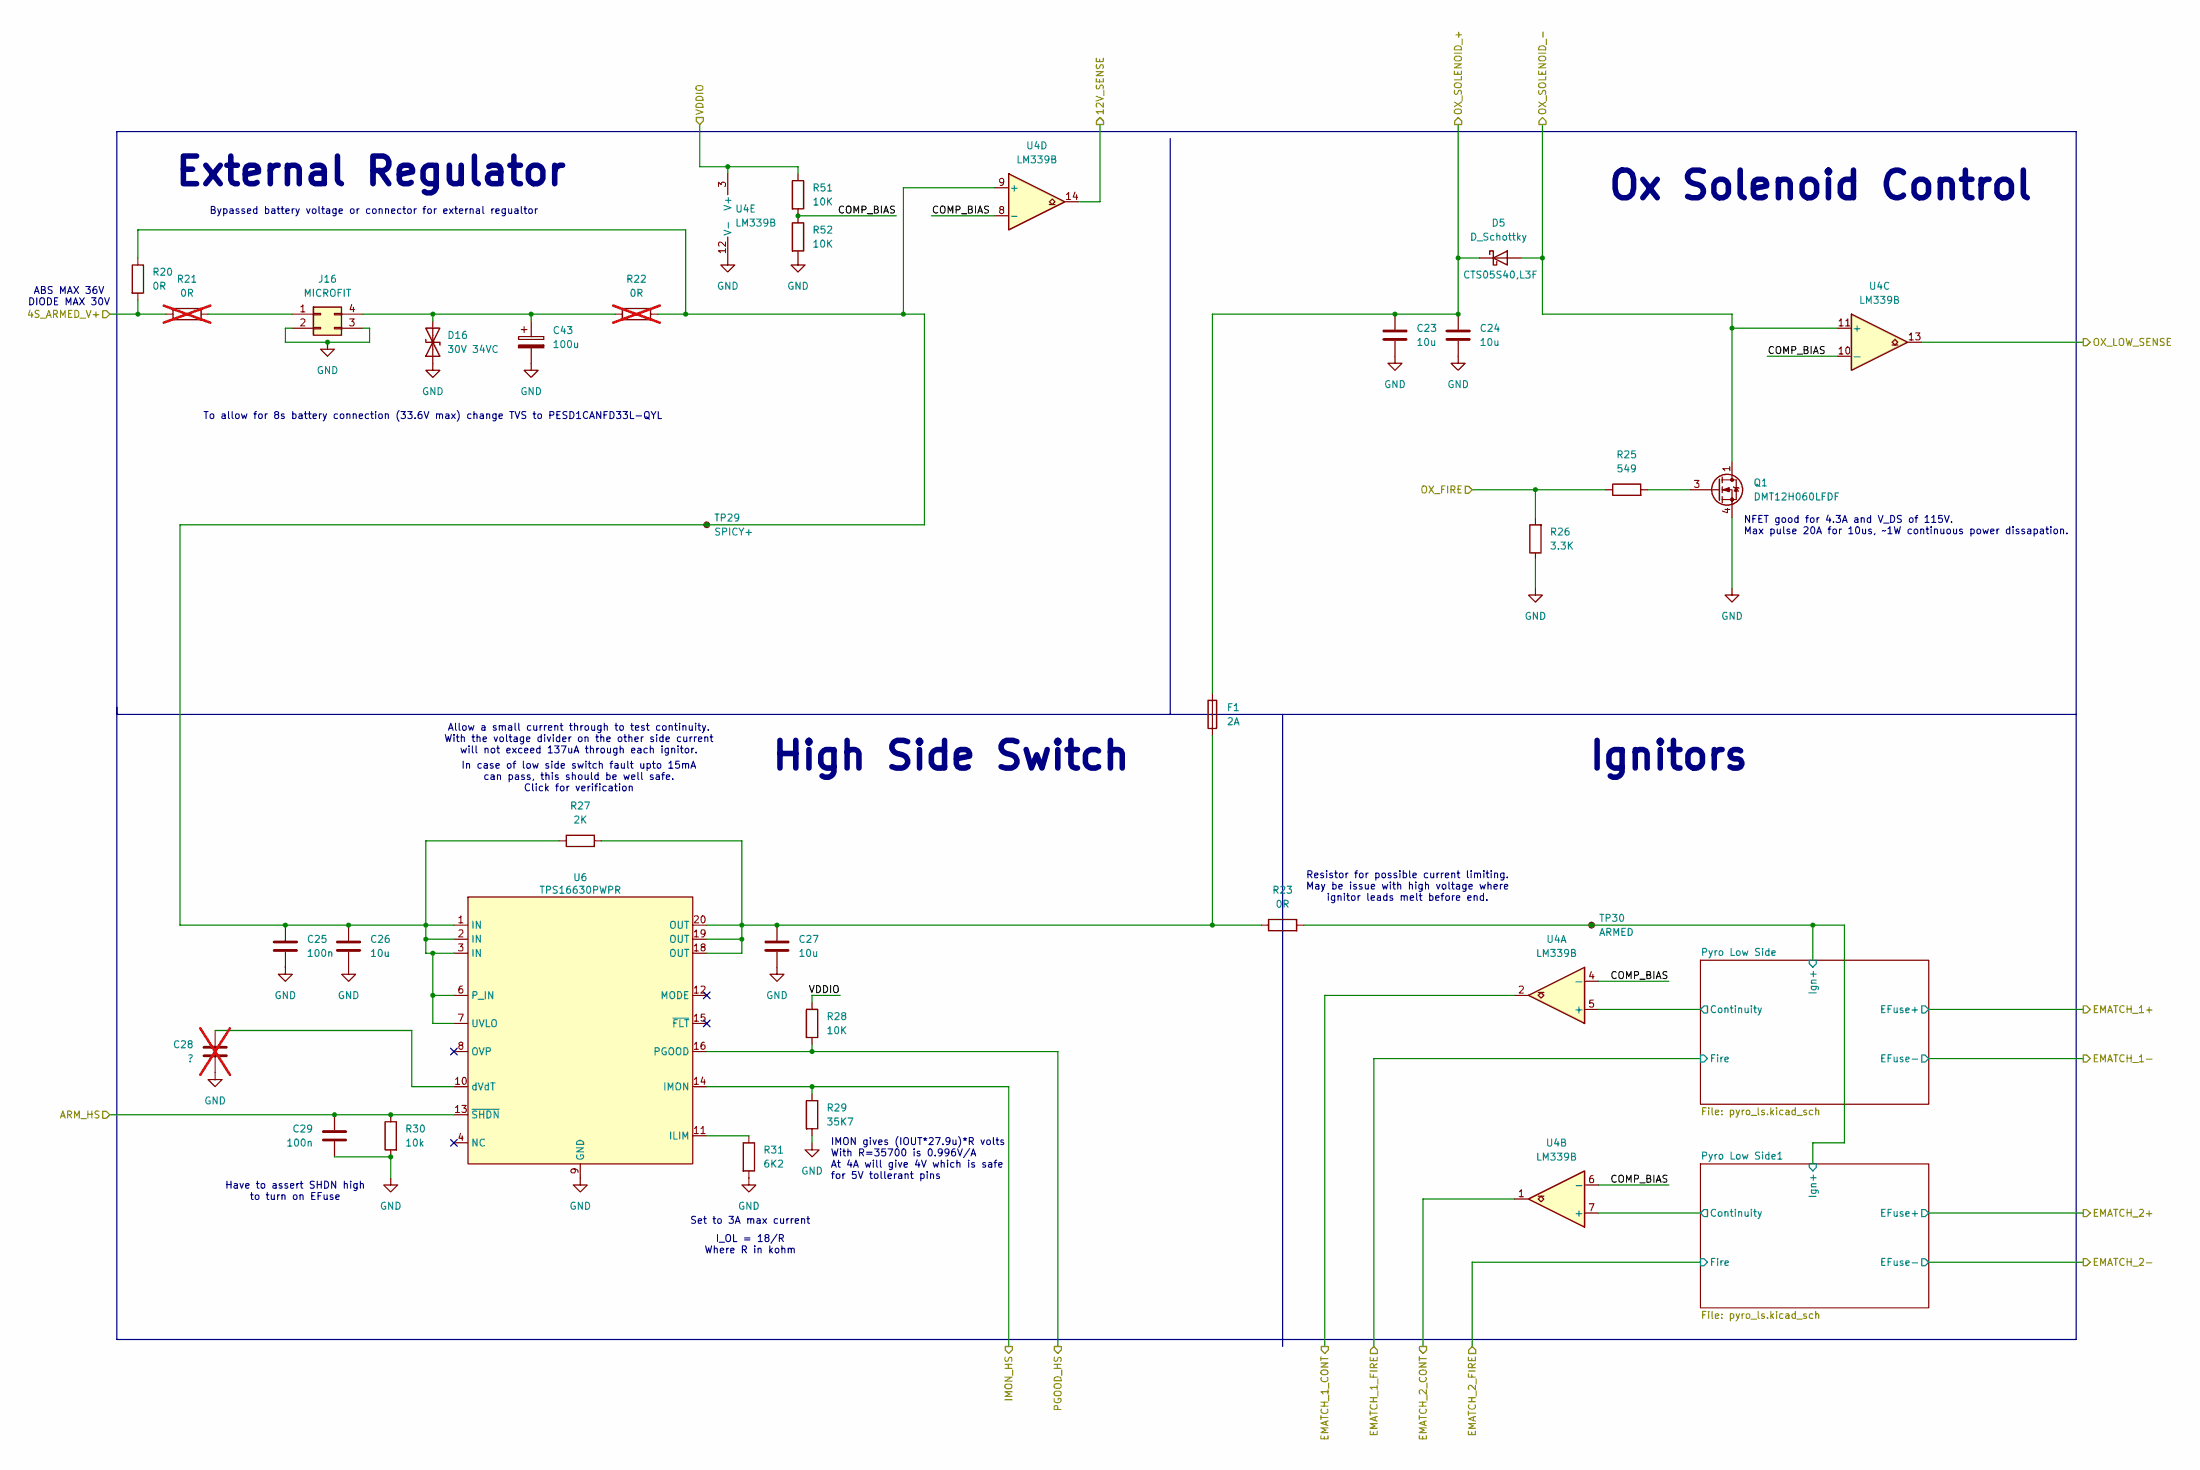
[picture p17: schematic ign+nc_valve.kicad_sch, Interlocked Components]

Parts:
C23, C24, C26, C27: 10u; C_1206_3216Metric
C25, C29: 100n; C_0603_1608Metric
C28: ?; C_0603_1608Metric; not fitted
C43: 100u; CP_Elec_8x10.5; MPN A768KS107M1HLAE030
D5: D_Schottky; D_SOD-882; MPN CTS05S40,L3F
D16: 30V 34VC; D_SOD-882; MPN PESD1CANFD30L-QYL
F1: 2A; Fuse_1206_3216Metric
J16: MICROFIT; Molex_Micro-Fit_3.0_43045-0412_2x02_P3.00mm_Vertical; MPN 0430450412
Q1: DMT12H060LFDF; Diodes_UDFN2020-6_Type-F; MPN DMT12H060LFDF-7
R20, R23: 0R; R_1206_3216Metric
R21, R22: 0R; R_1206_3216Metric; not fitted
R25: 549; R_0603_1608Metric
R26: 3.3K; R_0603_1608Metric
R27: 2K; R_0603_1608Metric
R28, R51, R52: 10K; R_0603_1608Metric
R29: 35K7; R_0603_1608Metric
R30: 10k; R_0603_1608Metric
R31: 6K2; R_0603_1608Metric
TP29: SPICY+; TestPoint_Pad_1.5x1.5mm
TP30: ARMED; TestPoint_Pad_1.5x1.5mm
U4: LM339B; TSSOP-14_4.4x5mm_P0.65mm; MPN LM339BIPWR
U6: TPS16630PWPR; HTSSOP-20-1EP_4.4x6.5mm_P0.65mm_EP3.4x6.5mm_Mask2.96x2.96mm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; MPN TPS16630PWPR

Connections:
+3V3: R28.1, R51.1, U4.3 (V+); also elsewhere on the board
/4S_V+: R20.2, R21.1; also elsewhere on the board
/12V_SENSE: U4.14; also elsewhere on the board
/ARM_HS: C29.1, R30.1, U6.13 (~SHDN); also elsewhere on the board
/Connectors/EMATCH_1+: R23.2, TP30.1; also elsewhere on the board
/Connectors/SOLENOID+: C23.1, C24.1, D5.1 (K), F1.2; also elsewhere on the board
/Connectors/SOLENOID-: D5.2 (A), Q1.1, Q1.2 (D), Q1.5 (D), Q1.6 (D), Q1.7 (D), U4.11 (+); also elsewhere on the board
/EMATCH_1_CONT: U4.2; also elsewhere on the board
/EMATCH_2_CONT: U4.1; also elsewhere on the board
/IMON_HS: R29.1, U6.14 (IMON); also elsewhere on the board
/Interlocked/COMP_BIAS: R51.2, R52.1, U4.4 (-), U4.6 (-), U4.8 (-), U4.10 (-)
/Interlocked/Pyro Low Side1/Continuity: U4.7 (+); also elsewhere on the board
/Interlocked/Pyro Low Side/Continuity: U4.5 (+); also elsewhere on the board
/OX_FIRE: R25.1, R26.2; also elsewhere on the board
/OX_LOW_SENSE: U4.13; also elsewhere on the board
/PGOOD_HS: R28.2, U6.16 (PGOOD); also elsewhere on the board
GND: C23.2, C24.2, C25.2, C26.2, C27.2, C28.2, C29.2, C43.2, D16.1 (A1), J16.2, J16.3, Q1.4, Q1.8 (S), R26.1, R29.2, R30.2, R31.2, R52.2, U4.12 (V-), U6.9 (GND), U6.21 (GND); also elsewhere on the board
unnamed: C27.1, F1.1, R23.1, R27.2, U6.18 (OUT), U6.19 (OUT), U6.20 (OUT)
unnamed: C43.1, D16.2 (A2), J16.4, R22.1
unnamed: J16.1, R21.2
unnamed: Q1.3, R25.2
unnamed: C25.1, C26.1, R20.1, R22.2, R27.1, TP29.1, U4.9 (+), U6.1 (IN), U6.2 (IN), U6.3 (IN), U6.6 (P_IN), U6.7 (UVLO)
unnamed: R31.1, U6.11 (ILIM)
unnamed: C28.1, U6.10 (dVdT)

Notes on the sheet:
ABS MAX 36V DIODE MAX 30V
Have to assert SHDN high to turn on EFuse
External Regulator
NFET good for 4.3A and V_DS of 115V. Max pulse 20A for 10us, ~1W continuous power dissapation.
Set to 3A max current
To allow for 8s battery connection (33.6V max) change TVS to PESD1CANFD33L-QYL
Ox Solenoid Control
Ignitors
Bypassed battery voltage or connector for external regualtor
I_OL = 18/R Where R in kohm
Resistor for possible current limiting. May be issue with high voltage where ignitor leads melt before end.
In case of low side switch fault upto 15mA can pass, this should be well safe. Click for verification
Allow a small current through to test continuity. With the voltage divider on the other side current will not exceed 137uA through each ignitor.
IMON gives (IOUT*27.9u)*R volts With R=35700 is 0.996V/A At 4A will give 4V which is safe for 5V tollerant pins
High Side Switch

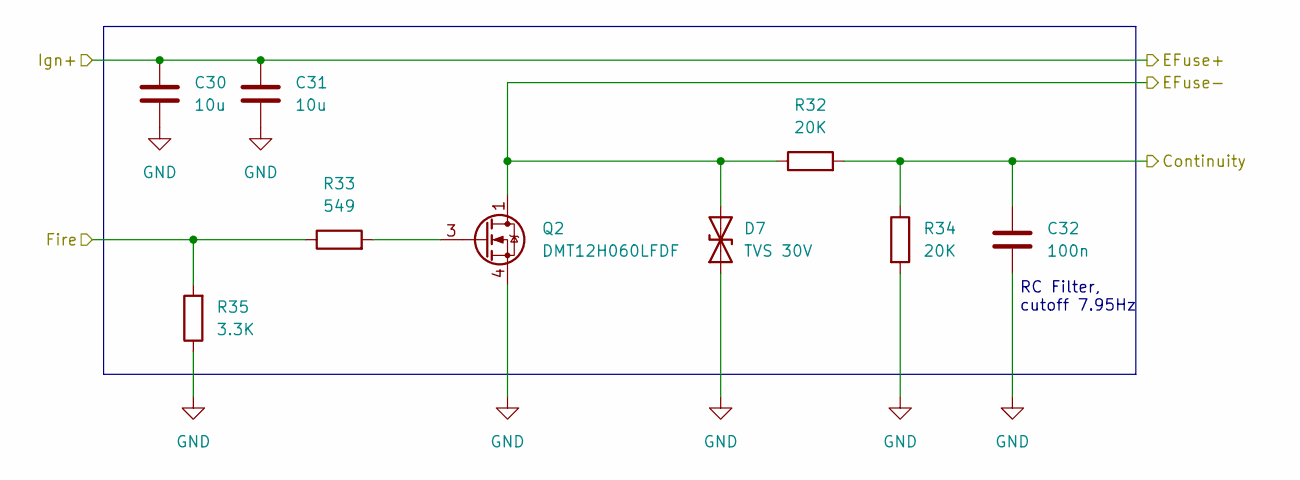
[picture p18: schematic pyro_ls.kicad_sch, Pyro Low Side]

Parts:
C30, C31: 10u; C_1206_3216Metric
C32: 100n; C_0603_1608Metric
D7: TVS 30V; D_SOD-882; MPN PESD1CANFD30L-QYL
Q2: DMT12H060LFDF; Diodes_UDFN2020-6_Type-F; MPN DMT12H060LFDF-7
R32, R34: 20K; R_0603_1608Metric
R33: 549; R_0603_1608Metric
R35: 3.3K; R_0603_1608Metric

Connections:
/Connectors/EMATCH_1+: C30.1, C31.1; also elsewhere on the board
/Connectors/EMATCH_2-: D7.2 (A2), Q2.1, Q2.2 (D), Q2.5 (D), Q2.6 (D), Q2.7 (D), R32.1; also elsewhere on the board
/EMATCH_2_FIRE: R33.1, R35.2; also elsewhere on the board
/Interlocked/Pyro Low Side1/Continuity: C32.1, R32.2, R34.1; also elsewhere on the board
GND: C30.2, C31.2, C32.2, D7.1 (A1), Q2.4, Q2.8 (S), R34.2, R35.1; also elsewhere on the board
unnamed: Q2.3, R33.2

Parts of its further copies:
C33, C34: 10u; C_1206_3216Metric
C35: 100n; C_0603_1608Metric
D15: TVS 30V; D_SOD-882; MPN PESD1CANFD30L-QYL
Q3: DMT12H060LFDF; Diodes_UDFN2020-6_Type-F; MPN DMT12H060LFDF-7
R36, R38: 20K; R_0603_1608Metric
R37: 549; R_0603_1608Metric
R39: 3.3K; R_0603_1608Metric

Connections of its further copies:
/Connectors/EMATCH_1+: C33.1, C34.1; also elsewhere on the board
/Connectors/EMATCH_1-: D15.2 (A2), Q3.1, Q3.2 (D), Q3.5 (D), Q3.6 (D), Q3.7 (D), R36.1; also elsewhere on the board
/EMATCH_1_FIRE: R37.1, R39.2; also elsewhere on the board
/Interlocked/Pyro Low Side/Continuity: C35.1, R36.2, R38.1; also elsewhere on the board
GND: C33.2, C34.2, C35.2, D15.1 (A1), Q3.4, Q3.8 (S), R38.2, R39.1; also elsewhere on the board
unnamed: Q3.3, R37.2

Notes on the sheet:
RC Filter, cutoff 7.95Hz

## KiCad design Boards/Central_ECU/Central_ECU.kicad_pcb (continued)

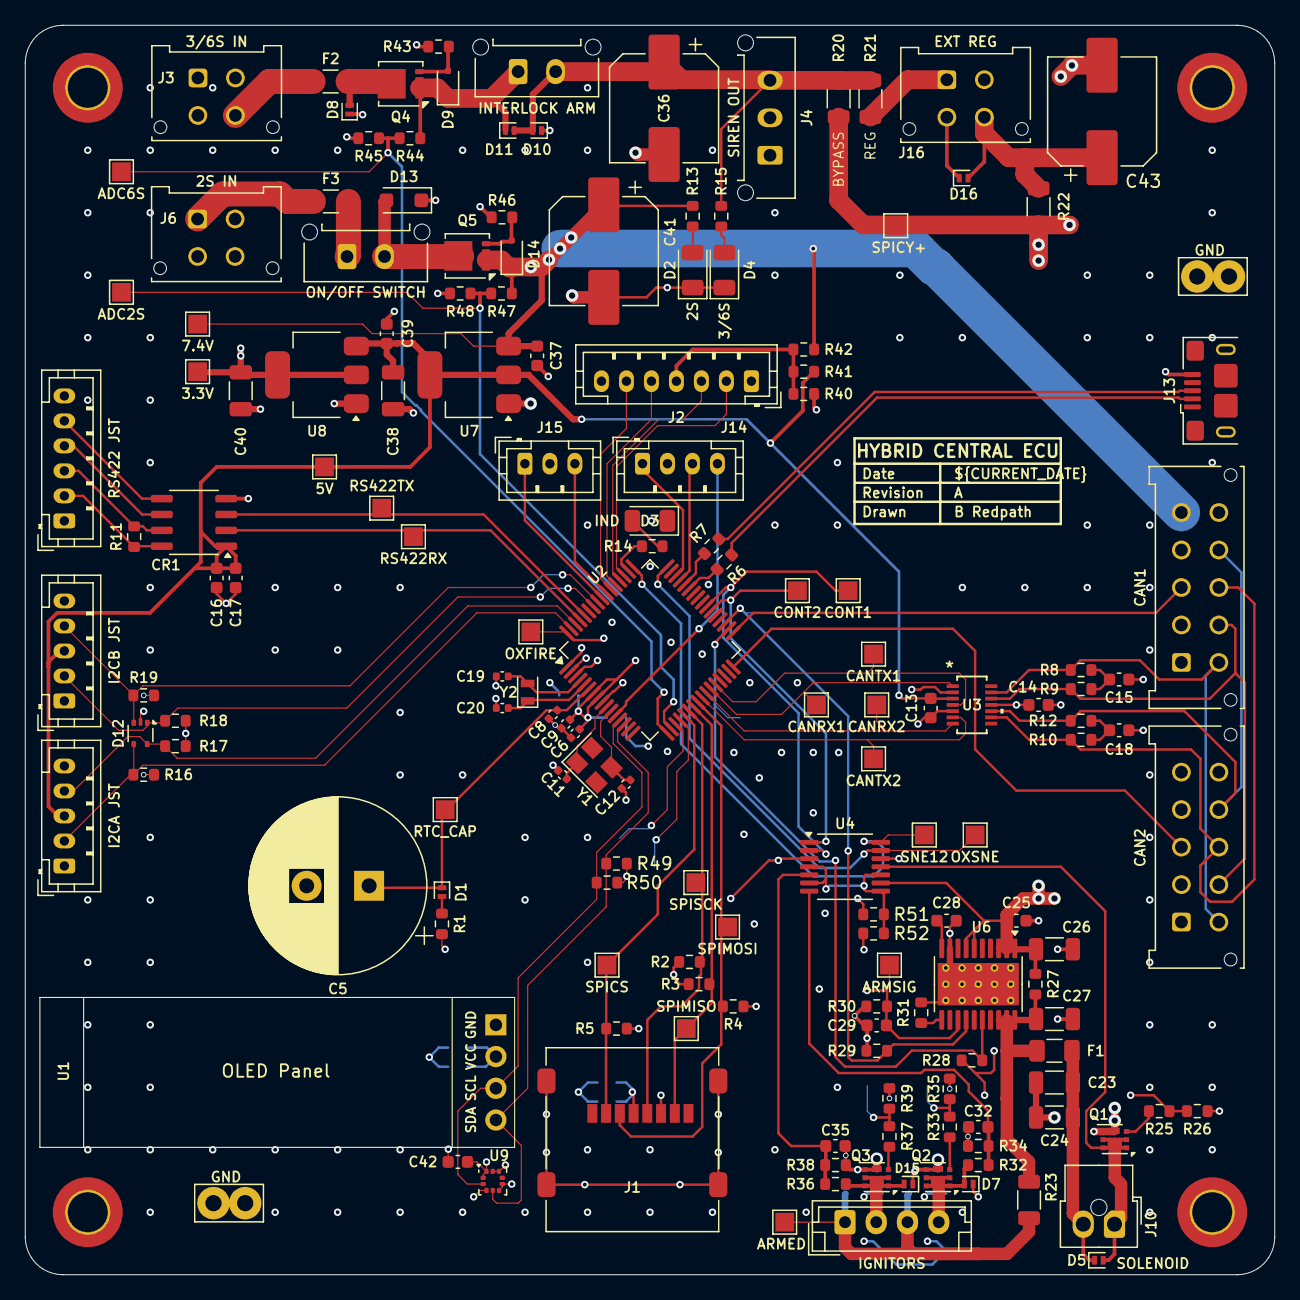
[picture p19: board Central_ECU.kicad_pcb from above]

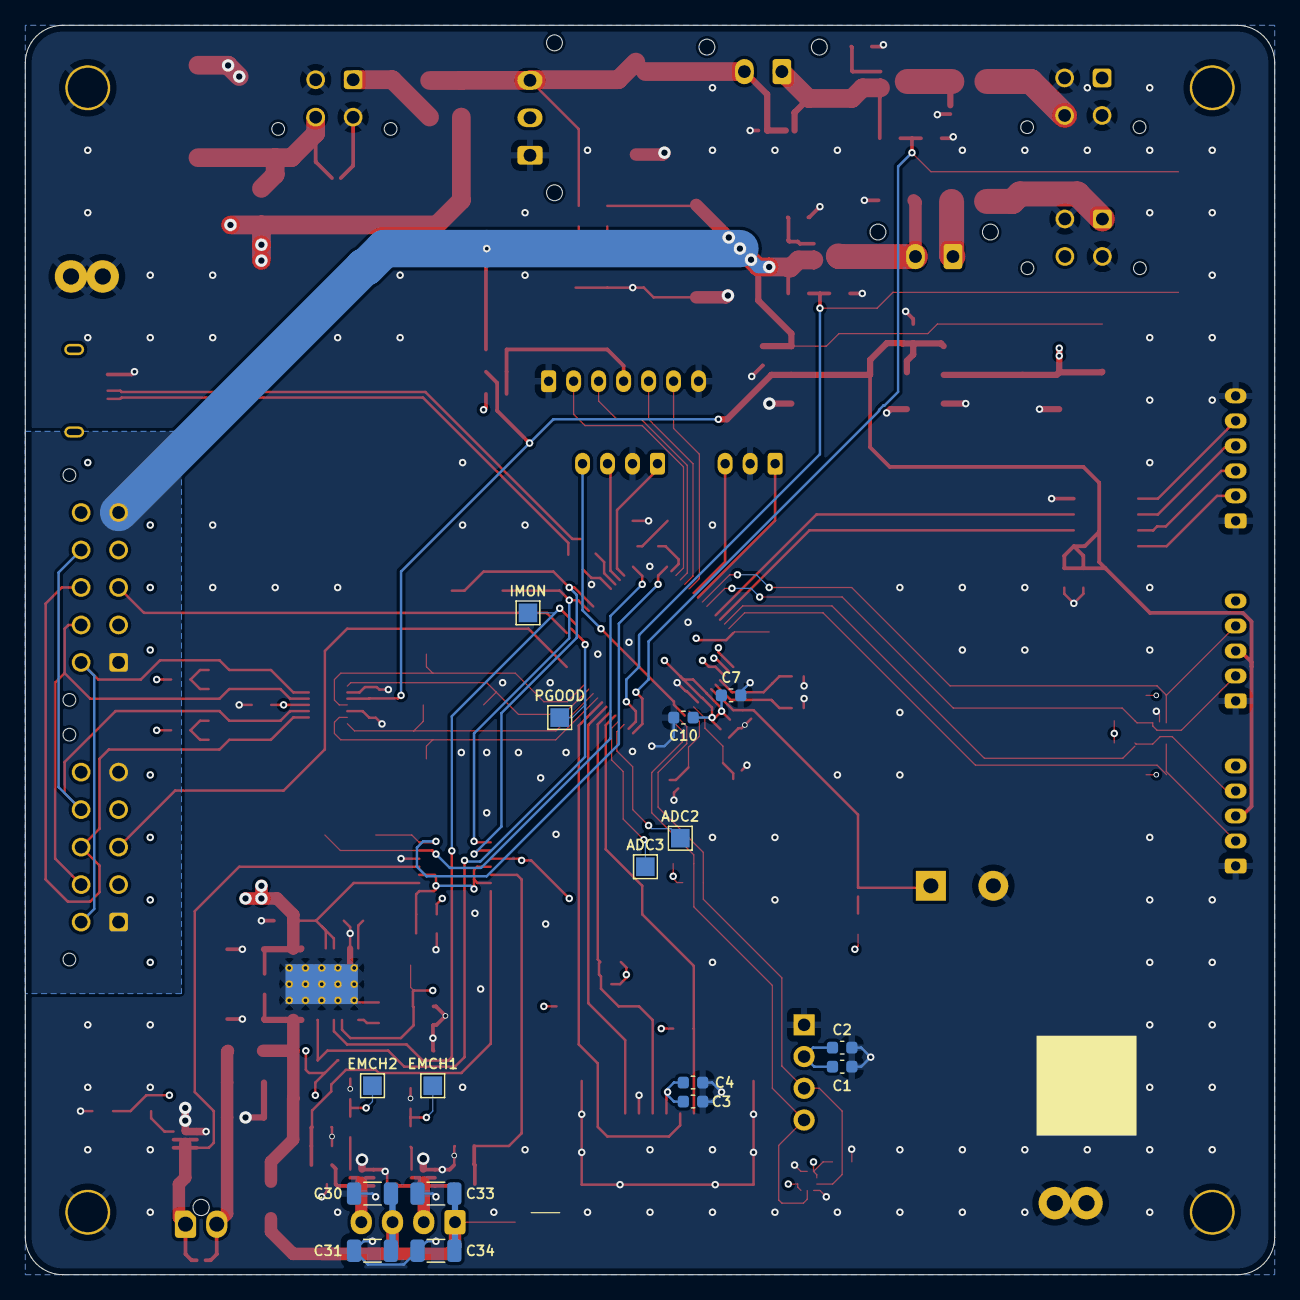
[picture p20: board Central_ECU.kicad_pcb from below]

Board: 4 copper layers, 100.0 x 100.0 mm, 180 parts (16 on the bottom side), 93 nets.

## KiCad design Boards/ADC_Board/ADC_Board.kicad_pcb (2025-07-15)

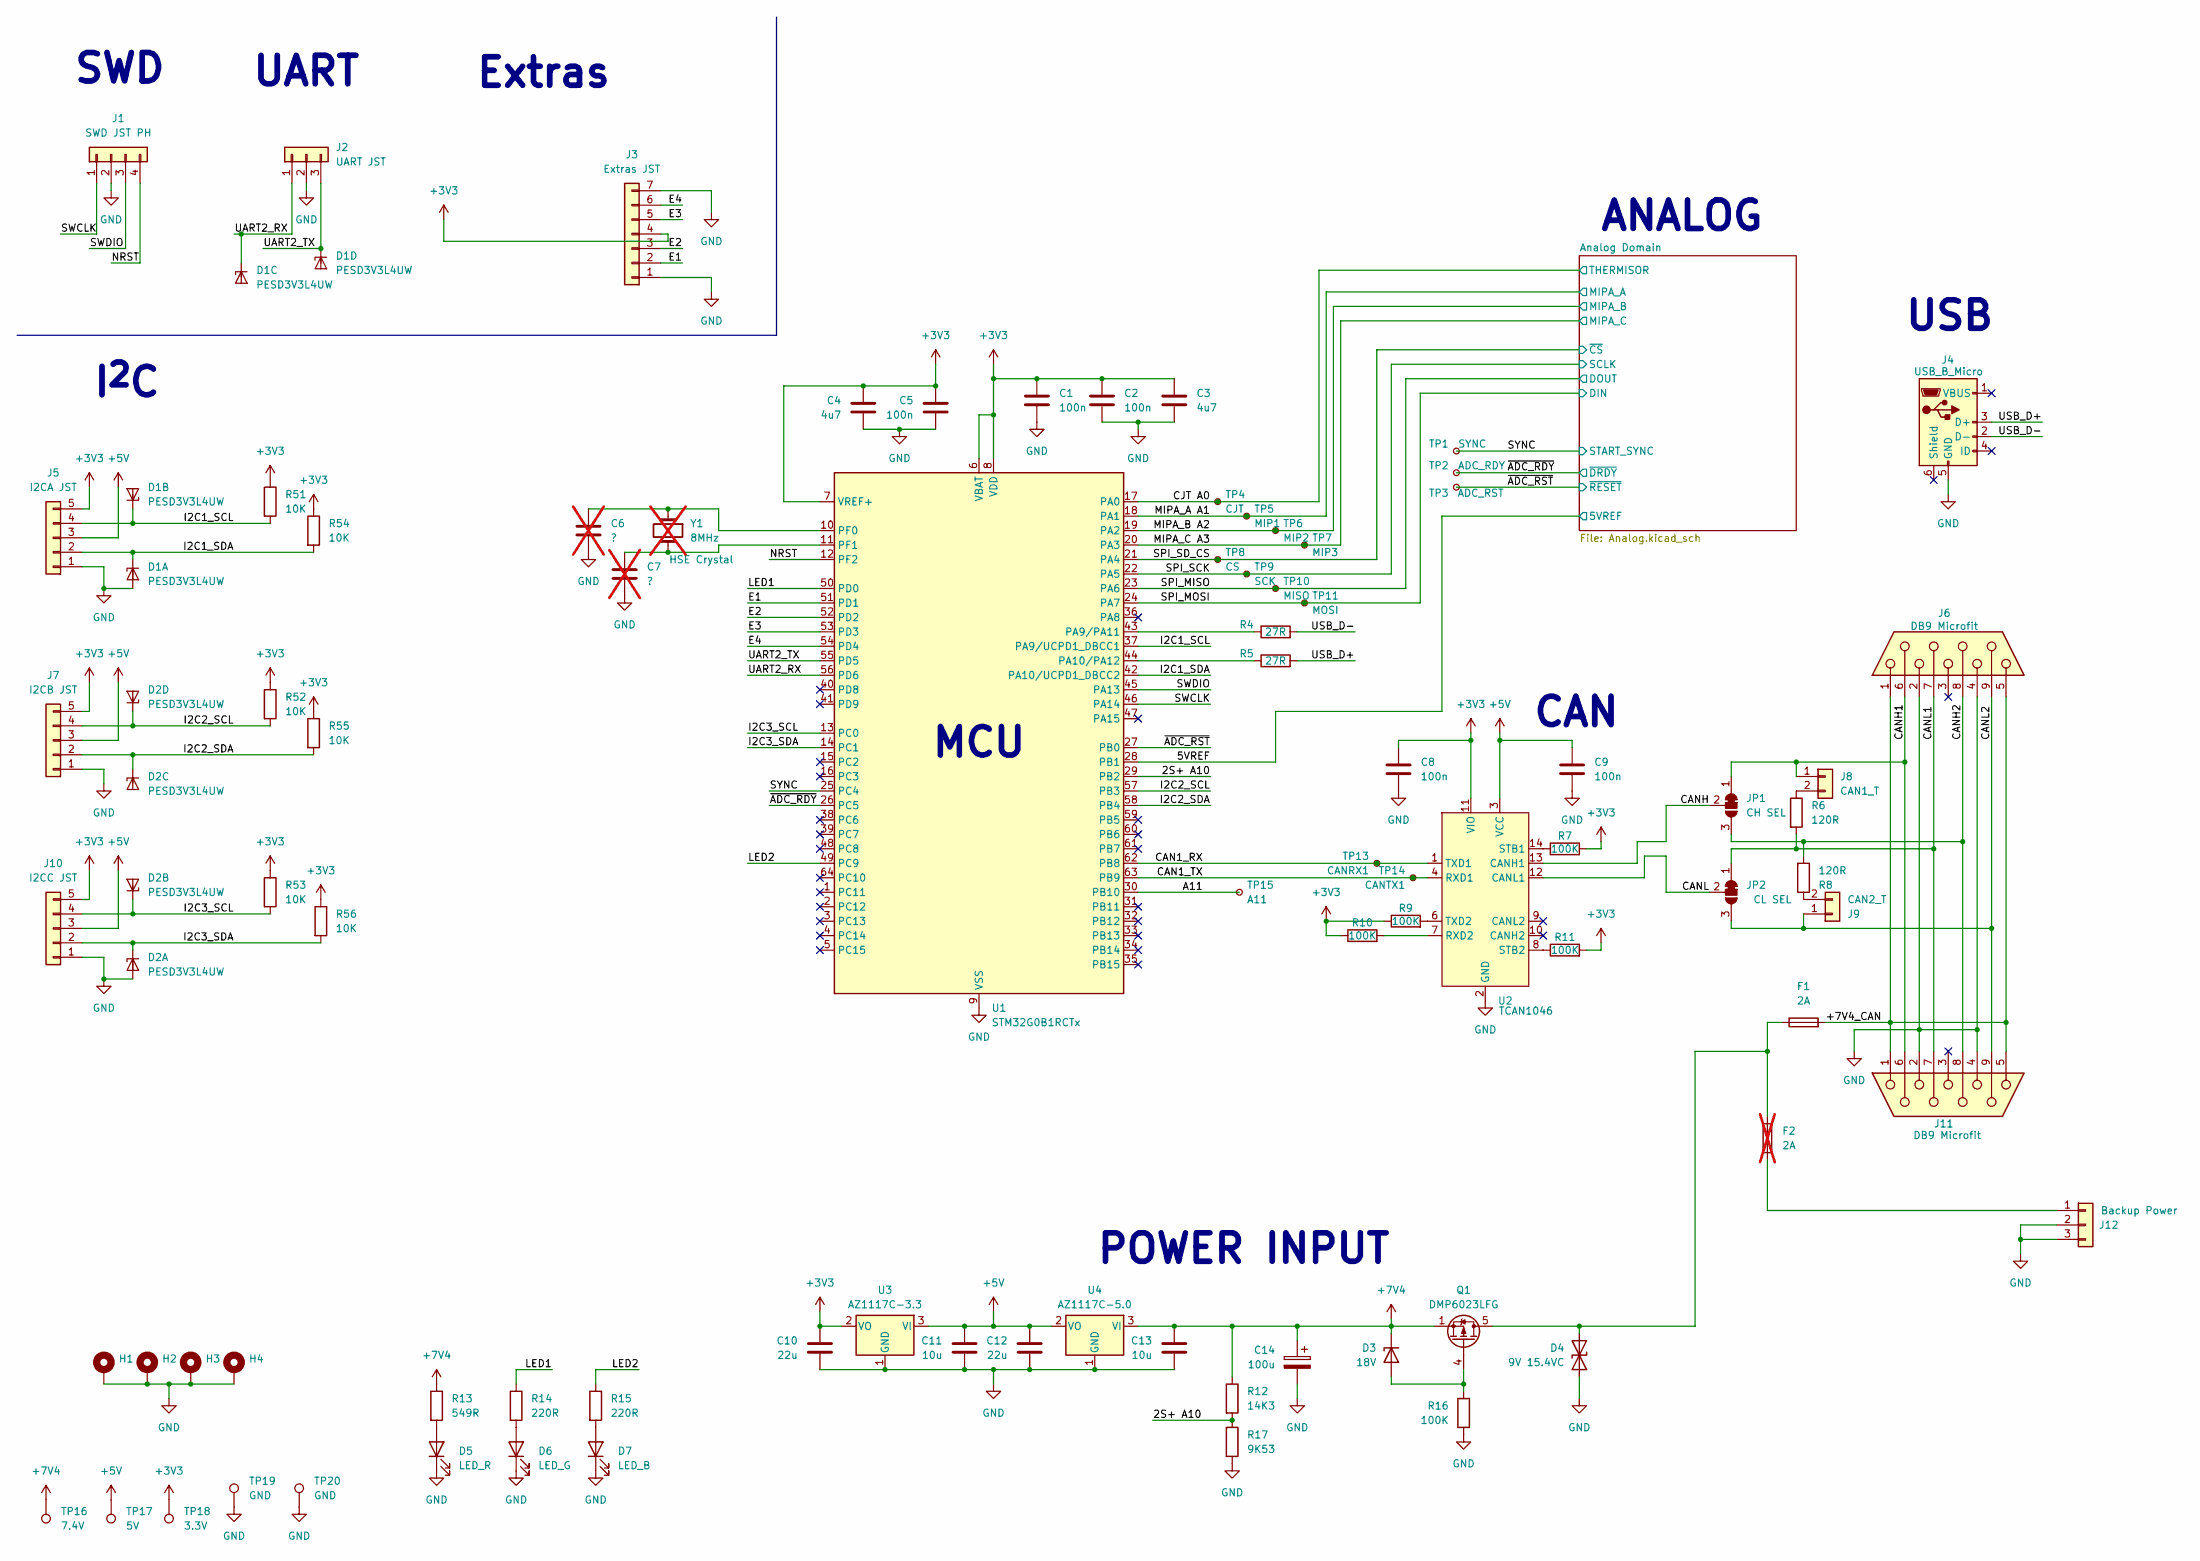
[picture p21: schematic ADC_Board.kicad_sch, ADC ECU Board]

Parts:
C1, C2, C5: 100n; C_0402_1005Metric
C3, C4: 4u7; C_0603_1608Metric
C6, C7: ?; C_0402_1005Metric; not fitted
C8, C9: 100n; C_0603_1608Metric
C10, C12: 22u; C_1206_3216Metric
C11, C13: 10u; C_0603_1608Metric
C14: 100u; CP_Elec_8x10.5; MPN A768KS107M1HLAE030
D1, D2: PESD3V3L4UW; SOT-665
D3: 18V; D_SOD-323F; MPN MM3Z18VB
D4: 9V 15.4VC; D_SOD-123F; MPN SMF9.0CA
D5: LED_R; LED_1206_3216Metric; MPN LTST-C150KRKT
D6: LED_G; LED_1206_3216Metric; MPN LTST-C150KGKT
D7: LED_B; LED_1206_3216Metric; MPN LTST-C150TBKT
F1: 2A; Fuse_1206_3216Metric
F2: 2A; Fuse_1206_3216Metric; not fitted
H1, H2, H3, H4: MountingHole_3.2mm_M3_DIN965_Pad_TopOnly
J1: SWD JST PH; JST_PH_B4B-PH-K_1x04_P2.00mm_Vertical; MPN B4B-PH-K-S
J2: UART JST; JST_PH_B3B-PH-K_1x03_P2.00mm_Vertical; MPN B3B-PH-K-S
J3: Extras JST; JST_PH_B7B-PH-K_1x07_P2.00mm_Vertical; MPN B7B-PH-K-S
J4: USB_B_Micro; USB_Micro-B_Amphenol_10118193-0001LF_Horizontal; MPN 10118193-0001LF
J5: I2CA JST; JST_PH_B5B-PH-K_1x05_P2.00mm_Vertical; MPN B6B-PH-K-S
J6: DB9 Microfit; DSUB-9_Pins_Horizontal_P2.77x2.84mm_EdgePinOffset7.70mm_Hou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; MPN A-DS 09 A/KG-T2S
J7: I2CB JST; JST_PH_B5B-PH-K_1x05_P2.00mm_Vertical; MPN B5B-PH-K-S
J8: CAN1_T; PinHeader_1x02_P2.54mm_Vertical
J9: CAN2_T; PinHeader_1x02_P2.54mm_Vertical
J10: I2CC JST; JST_PH_B5B-PH-K_1x05_P2.00mm_Vertical; MPN B5B-PH-K-S
J11: DB9 Microfit; DSUB-9_Pins_Horizontal_P2.77x2.84mm_EdgePinOffset7.70mm_Hou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; MPN A-DF 09 A/KG-T2S
J12: Backup Power; Molex_Micro-Fit_3.0_43650-0315_1x03_P3.00mm_Vertical; MPN 436500315
JP1: CH SEL; SolderJumper-3_P1.3mm_Bridged12_RoundedPad1.0x1.5mm
JP2: CL SEL; SolderJumper-3_P1.3mm_Bridged12_RoundedPad1.0x1.5mm
Q1: DMP6023LFG; Diodes_PowerDI3333-8; MPN DMP6023LFG-7
R4, R5: 27R; R_0603_1608Metric
R6, R8: 120R; R_0603_1608Metric
R7, R9, R10, R11, R16: 100K; R_0603_1608Metric
R12: 14K3; R_0603_1608Metric
R13: 549R; R_0603_1608Metric
R14, R15: 220R; R_0603_1608Metric
R17: 9K53; R_0603_1608Metric
R51, R52, R53, R54, R55, R56: 10K; R_0603_1608Metric
TP1: SYNC; TestPoint_Pad_D1.0mm
TP2: ADC_RDY; TestPoint_Pad_D1.0mm
TP3: ADC_RST; TestPoint_Pad_D1.0mm
TP4: CJT; TestPoint_Pad_D1.0mm
TP5: MIP1; TestPoint_Pad_D1.0mm
TP6: MIP2; TestPoint_Pad_D1.0mm
TP7: MIP3; TestPoint_Pad_D1.0mm
TP8: CS; TestPoint_Pad_D1.0mm
TP9: SCK; TestPoint_Pad_D1.0mm
TP10: MISO; TestPoint_Pad_D1.0mm
TP11: MOSI; TestPoint_Pad_D1.0mm
TP13: CANRX1; TestPoint_Pad_D1.0mm
TP14: CANTX1; TestPoint_Pad_D1.0mm
TP15: A11; TestPoint_Pad_D1.0mm
TP16: 7.4V; TestPoint_Pad_D1.0mm
TP17: 5V; TestPoint_Pad_D1.0mm
TP18: 3.3V; TestPoint_Pad_D1.0mm
TP19, TP20: GND; TestPoint_Bridge_Pitch2.54mm_Drill1.3mm
U1: STM32G0B1RCTx; LQFP-64_10x10mm_P0.5mm; MPN STM32G0B1RCT6
U2: TCAN1046; SOT23_DYY_TEX; MPN TCAN1046AVDYYRQ1
U3: AZ1117C-3.3; SOT-223-3_TabPin2; MPN AZ1117CH-3.3TRG1
U4: AZ1117C-5.0; SOT-223-3_TabPin2; MPN AZ1117CH-5.0TRG1
Y1: 8MHz; Crystal_SMD_Abracon_ABM8G-4Pin_3.2x2.5mm; not fitted

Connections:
+3V3: C1.1, C2.1, C3.1, C4.1, C5.1, C8.1, C10.1, J3.4, J5.5, J7.5, J10.5, R7.2, R9.1, R10.1, R11.2, R51.1, R52.1, R53.1, R54.1, R55.1, R56.1, TP18.1, U1.6 (VBAT), U1.7 (VREF+), U1.8 (VDD), U2.11 (VIO), U3.2 (VO); also elsewhere on the board
+5V: C9.1, C11.1, C12.1, J5.3, J7.3, J10.3, TP17.1, U2.3 (VCC), U3.3 (VI), U4.2 (VO); also elsewhere on the board
+7V4: C13.1, C14.1, D3.1 (K), Q1.1 (S), Q1.2 (S), Q1.3 (S), R12.1, R13.1, TP16.1, U4.3 (VI)
/2S+ A10: R12.2, R17.1, U1.29 (PB2)
/5VREF: U1.28 (PB1); also elsewhere on the board
/+7V4_CAN: F1.2, J6.1, J6.5, J11.1, J11.5
/A11: TP15.1, U1.30 (PB10)
/CAN1_RX: TP13.1, U1.62 (PB8), U2.1 (TXD1)
/CAN1_TX: TP14.1, U1.63 (PB9), U2.4 (RXD1)
/CANH: JP1.2 (C), U2.13 (CANH1)
/CANH1: J6.6, J8.1, J11.6, JP1.1 (A)
/CANH2: J6.8, J11.8, JP1.3 (B), R8.2
/CANL: JP2.2 (C), U2.12 (CANL1)
/CANL1: J6.7, J11.7, JP2.1 (A), R6.2
/CANL2: J6.9, J9.1, J11.9, JP2.3 (B)
/CJT A0: TP4.1, U1.17 (PA0); also elsewhere on the board
/E1: J3.2, U1.51 (PD1)
/E2: J3.3, U1.52 (PD2)
/E3: J3.5, U1.53 (PD3)
/E4: J3.6, U1.54 (PD4)
/I2C1_SCL: D1.3 (K2), J5.4, R51.2, U1.37 (PA9/UCPD1_DBCC1)
/I2C1_SDA: D1.1 (K1), J5.2, R54.2, U1.42 (PA10/UCPD1_DBCC2)
/I2C2_SCL: D2.5 (K4), J7.4, R52.2, U1.57 (PB3)
/I2C2_SDA: D2.4 (K3), J7.2, R55.2, U1.58 (PB4)
/I2C3_SCL: D2.3 (K2), J10.4, R53.2, U1.13 (PC0)
/I2C3_SDA: D2.1 (K1), J10.2, R56.2, U1.14 (PC1)
/LED1: R14.1, U1.50 (PD0)
/LED2: R15.1, U1.49 (PC9)
/MIPA_A A1: TP5.1, U1.18 (PA1); also elsewhere on the board
/MIPA_B A2: TP6.1, U1.19 (PA2); also elsewhere on the board
/MIPA_C A3: TP7.1, U1.20 (PA3); also elsewhere on the board
/NRST: J1.4, U1.12 (PF2)
/SPI_MISO: TP10.1, U1.23 (PA6); also elsewhere on the board
/SPI_MOSI: TP11.1, U1.24 (PA7); also elsewhere on the board
/SPI_SCK: TP9.1, U1.22 (PA5); also elsewhere on the board
/SPI_SD_CS: TP8.1, U1.21 (PA4); also elsewhere on the board
/SWCLK: J1.1, U1.46 (PA14)
/SWDIO: J1.3, U1.45 (PA13)
/SYNC: TP1.1, U1.25 (PC4); also elsewhere on the board
/UART2_RX: D1.4 (K3), J2.1, U1.56 (PD6)
/UART2_TX: D1.5 (K4), J2.3, U1.55 (PD5)
/USB_D+: J4.3 (D+), R5.2
/USB_D-: J4.2 (D-), R4.2
/~ADC_RDY: TP2.1, U1.26 (PC5); also elsewhere on the board
/~ADC_RST: TP3.1, U1.27 (PB0); also elsewhere on the board
GND: C1.2, C2.2, C3.2, C4.2, C5.2, C6.2, C7.2, C8.2, C9.2, C10.2, C11.2, C12.2, C13.2, C14.2, D1.2 (A), D2.2 (A), D4.1 (A1), D5.1 (K), D6.1 (K), D7.1 (K), H1.1, H2.1, H3.1, H4.1, J1.2, J2.2, J3.1, J3.7, J4.5 (GND), J5.1, J6.2, J6.4, J7.1, J10.1, J11.2, J11.4, J12.2, J12.3, R16.2, R17.2, TP19.1, TP20.1, U1.9 (VSS), U2.2 (GND), U2.5 (GND), U3.1 (GND), U4.1 (GND); also elsewhere on the board
unnamed: D3.2 (A), Q1.4 (G), R16.1
unnamed: D4.2 (A2), F1.1, F2.2, Q1.5 (D)
unnamed: D5.2 (A), R13.2
unnamed: D6.2 (A), R14.2
unnamed: D7.2 (A), R15.2
unnamed: J8.2, R6.1
unnamed: J9.2, R8.1
unnamed: F2.1, J12.1
unnamed: R4.1, U1.43 (PA9/PA11)
unnamed: R5.1, U1.44 (PA10/PA12)
unnamed: C6.1, U1.10 (PF0), Y1.1
unnamed: C7.1, U1.11 (PF1), Y1.3 (2)
unnamed: R10.2, U2.7 (RXD2)
unnamed: R7.1, U2.14 (STB1)
unnamed: R11.1, U2.8 (STB2)
unnamed: R9.2, U2.6 (TXD2)

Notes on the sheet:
ANALOG
SWD
POWER INPUT
UART
CAN
I^{2}C
Extras
USB
MCU

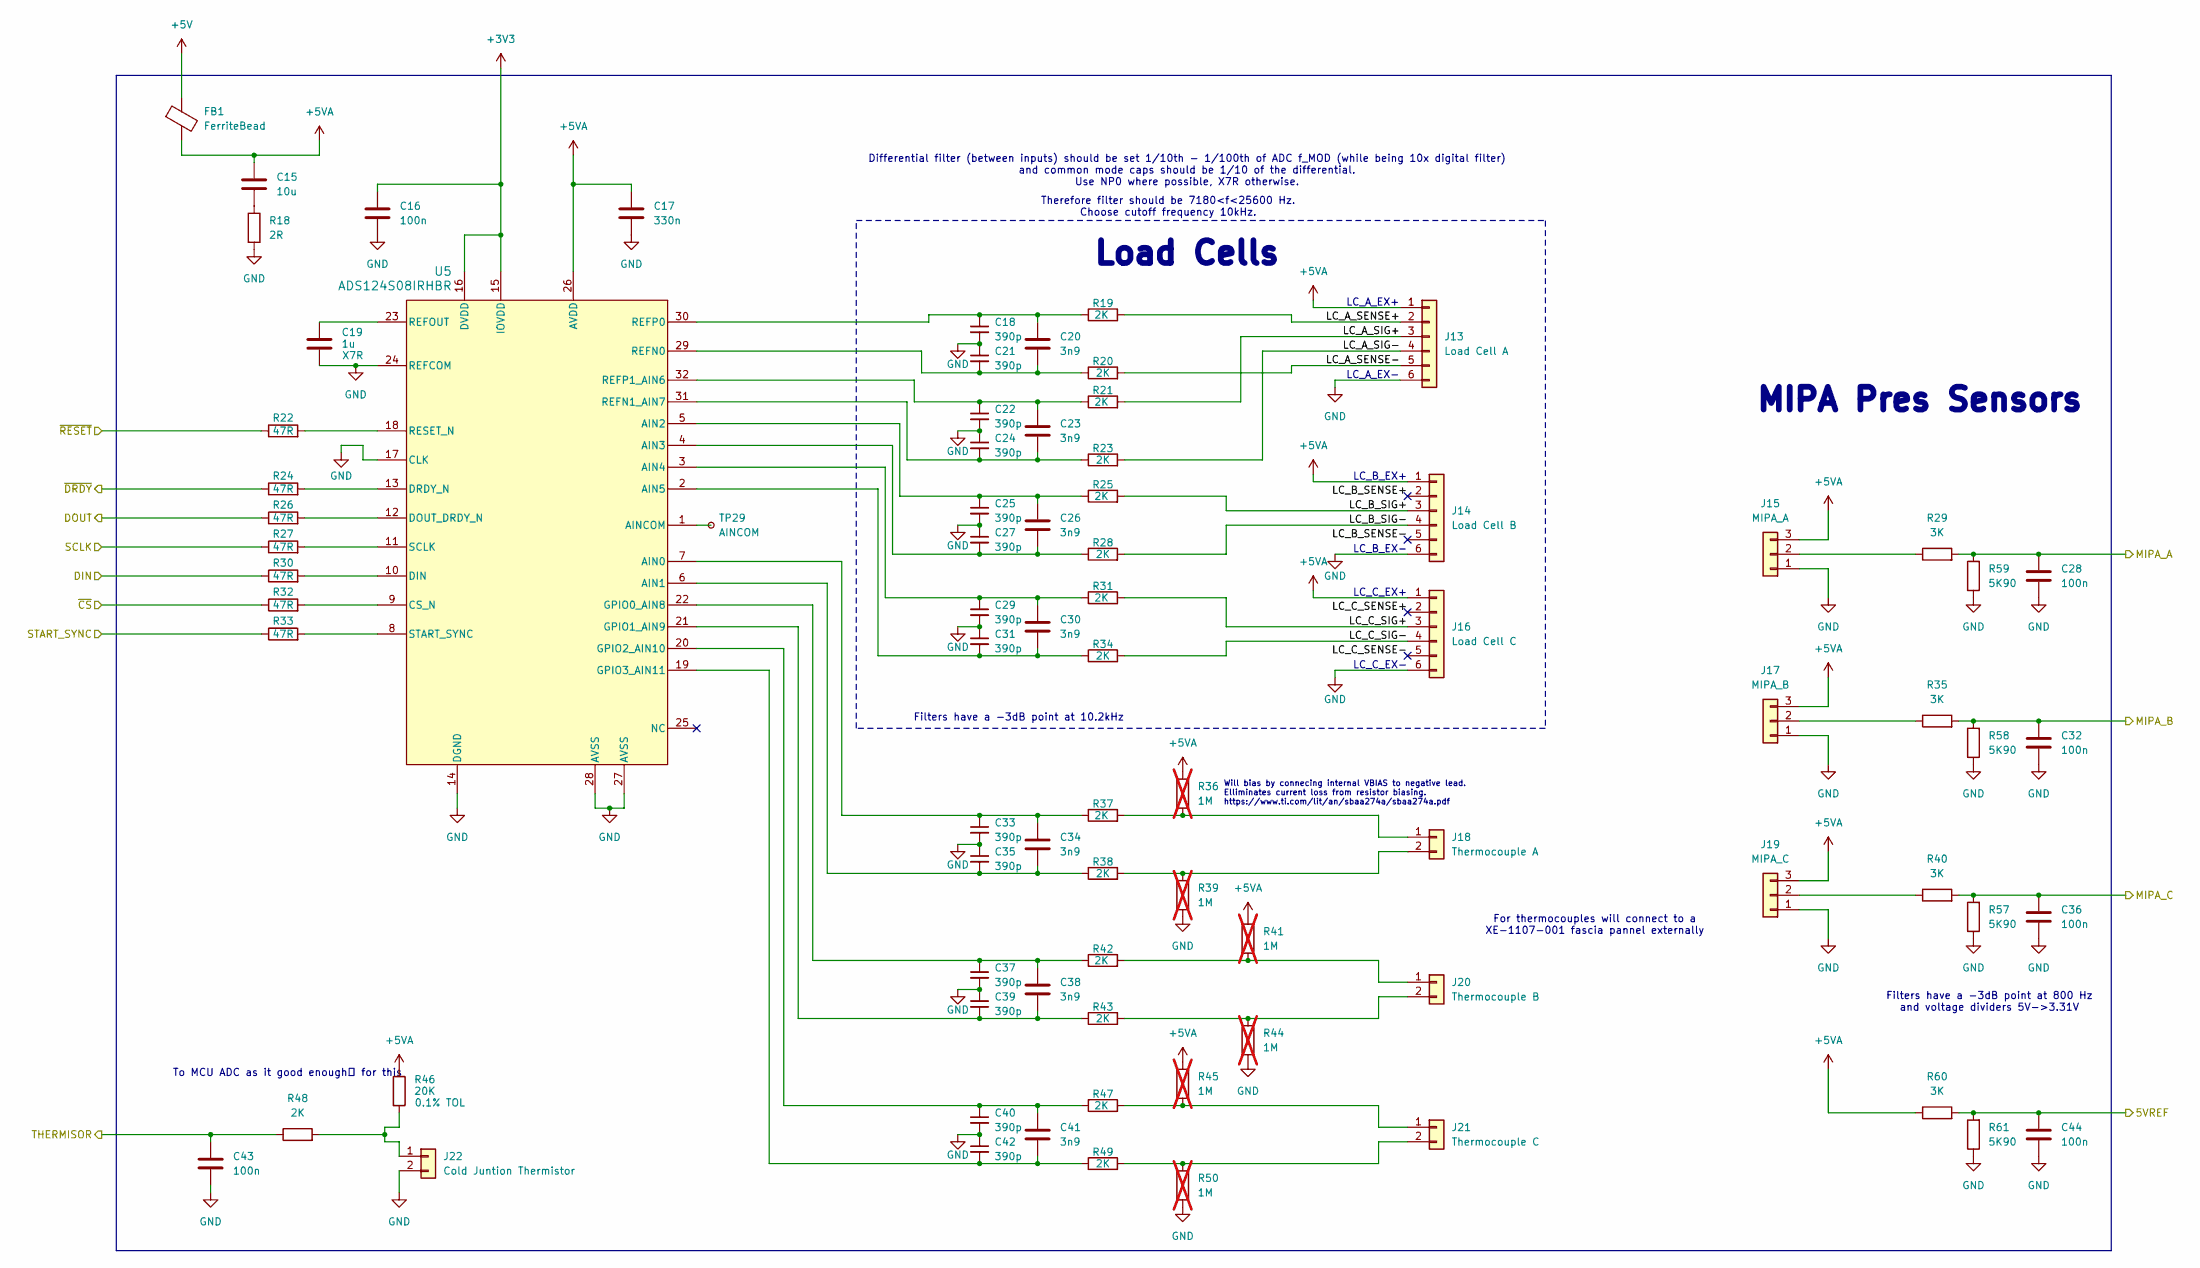
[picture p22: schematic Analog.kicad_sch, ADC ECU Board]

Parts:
C15: 10u; C_0603_1608Metric
C16, C28, C32, C36, C43, C44: 100n; C_0603_1608Metric
C17: 330n; C_0603_1608Metric
C18, C21, C22, C24, C25, C27, C29, C31, C33, C35, C37, C39, C40, C42: 390p; C_0402_1005Metric
C19: 1u; C_0603_1608Metric
C20, C23, C26, C30, C34, C38, C41: 3n9; C_0402_1005Metric
FB1: FerriteBead; L_1206_3216Metric; MPN BBUP00321611121Y00
J13: Load Cell A; JST_PH_B6B-PH-K_1x06_P2.00mm_Vertical
J14: Load Cell B; JST_PH_B6B-PH-K_1x06_P2.00mm_Vertical
J15: MIPA_A; JST_PH_B3B-PH-K_1x03_P2.00mm_Vertical
J16: Load Cell C; JST_PH_B6B-PH-K_1x06_P2.00mm_Vertical
J17: MIPA_B; JST_PH_B3B-PH-K_1x03_P2.00mm_Vertical
J18: Thermocouple A; JST_PH_B2B-PH-K_1x02_P2.00mm_Vertical
J19: MIPA_C; JST_PH_B3B-PH-K_1x03_P2.00mm_Vertical
J20: Thermocouple B; JST_PH_B2B-PH-K_1x02_P2.00mm_Vertical
J21: Thermocouple C; JST_PH_B2B-PH-K_1x02_P2.00mm_Vertical
J22: Cold Juntion Thermistor; JST_PH_B2B-PH-K_1x02_P2.00mm_Vertical
R18: 2R; R_0603_1608Metric
R19, R20, R21, R23, R25, R28, R31, R34, R37, R38, R42, R43, R47, R49: 2K; R_0402_1005Metric
R22, R24, R26, R27, R30, R32, R33: 47R; R_0603_1608Metric
R29, R35, R40, R60: 3K; R_0603_1608Metric
R36, R39, R41, R44, R45, R50: 1M; R_0402_1005Metric; not fitted
R46: 20K; R_0603_1608Metric
R48: 2K; R_0603_1608Metric
R57, R58, R59, R61: 5K90; R_0603_1608Metric
TP29: AINCOM; TestPoint_Pad_1.5x1.5mm
U5: ADS124S08IRHBR; QFN-32-1EP_5x5mm_P0.5mm_EP3.1x3.1mm; MPN ADS124S08IRHBR

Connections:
+3V3: C16.1, U5.15 (IOVDD), U5.16 (DVDD); also elsewhere on the board
+5V: FB1.1; also elsewhere on the board
+5VA: C15.1, C17.1, FB1.2, J13.1, J14.1, J15.3, J16.1, J17.3, J19.3, R36.1, R41.1, R45.1, R46.1, R60.1, U5.26 (AVDD)
/5VREF: C44.1, R60.2, R61.2; also elsewhere on the board
/Analog Domain/LC_A_SENSE+: J13.2, R19.2
/Analog Domain/LC_A_SENSE-: J13.5, R20.2
/Analog Domain/LC_A_SIG+: J13.3, R21.2
/Analog Domain/LC_A_SIG-: J13.4, R23.2
/Analog Domain/LC_B_SENSE+: J14.2
/Analog Domain/LC_B_SENSE-: J14.5
/Analog Domain/LC_B_SIG+: J14.3, R25.2
/Analog Domain/LC_B_SIG-: J14.4, R28.2
/Analog Domain/LC_C_SENSE+: J16.2
/Analog Domain/LC_C_SENSE-: J16.5
/Analog Domain/LC_C_SIG+: J16.3, R31.2
/Analog Domain/LC_C_SIG-: J16.4, R34.2
/CJT A0: C43.1, R48.1; also elsewhere on the board
/MIPA_A A1: C28.1, R29.2, R59.2; also elsewhere on the board
/MIPA_B A2: C32.1, R35.2, R58.2; also elsewhere on the board
/MIPA_C A3: C36.1, R40.2, R57.2; also elsewhere on the board
/SPI_MISO: R26.1; also elsewhere on the board
/SPI_MOSI: R30.1; also elsewhere on the board
/SPI_SCK: R27.1; also elsewhere on the board
/SPI_SD_CS: R32.1; also elsewhere on the board
/SYNC: R33.1; also elsewhere on the board
/~ADC_RDY: R24.1; also elsewhere on the board
/~ADC_RST: R22.1; also elsewhere on the board
GND: C16.2, C17.2, C18.2, C19.2, C21.1, C22.2, C24.1, C25.2, C27.1, C28.2, C29.2, C31.1, C32.2, C33.2, C35.1, C36.2, C37.2, C39.1, C40.2, C42.1, C43.2, C44.2, J13.6, J14.6, J15.1, J16.6, J17.1, J19.1, J22.2, R18.2, R39.2, R44.2, R50.2, R57.1, R58.1, R59.1, R61.1, U5.14 (DGND), U5.17 (CLK), U5.24 (REFCOM), U5.27 (AVSS), U5.28 (AVSS), U5.33 (PAD); also elsewhere on the board
unnamed: C15.2, R18.1
unnamed: J15.2, R29.1
unnamed: J17.2, R35.1
unnamed: J18.1, R36.2, R37.2
unnamed: J18.2, R38.2, R39.1
unnamed: J19.2, R40.1
unnamed: J20.1, R41.2, R42.2
unnamed: J20.2, R43.2, R44.1
unnamed: J21.1, R45.2, R47.2
unnamed: J21.2, R49.2, R50.1
unnamed: J22.1, R46.2, R48.2
unnamed: C33.1, C34.1, R37.1, U5.7 (AIN0)
unnamed: C34.2, C35.2, R38.1, U5.6 (AIN1)
unnamed: C25.1, C26.1, R25.1, U5.5 (AIN2)
unnamed: C26.2, C27.2, R28.1, U5.4 (AIN3)
unnamed: C29.1, C30.1, R31.1, U5.3 (AIN4)
unnamed: C30.2, C31.2, R34.1, U5.2 (AIN5)
unnamed: TP29.1, U5.1 (AINCOM)
unnamed: R32.2, U5.9 (CS_N)
unnamed: R30.2, U5.10 (DIN)
unnamed: R26.2, U5.12 (DOUT_DRDY_N)
unnamed: R24.2, U5.13 (DRDY_N)
unnamed: C37.1, C38.1, R42.1, U5.22 (GPIO0_AIN8)
unnamed: C38.2, C39.2, R43.1, U5.21 (GPIO1_AIN9)
unnamed: C40.1, C41.1, R47.1, U5.20 (GPIO2_AIN10)
unnamed: C41.2, C42.2, R49.1, U5.19 (GPIO3_AIN11)
unnamed: C20.2, C21.2, R20.1, U5.29 (REFN0)
unnamed: C23.2, C24.2, R23.1, U5.31 (REFN1_AIN7)
unnamed: C19.1, U5.23 (REFOUT)
unnamed: C18.1, C20.1, R19.1, U5.30 (REFP0)
unnamed: C22.1, C23.1, R21.1, U5.32 (REFP1_AIN6)
unnamed: R22.2, U5.18 (RESET_N)
unnamed: R27.2, U5.11 (SCLK)
unnamed: R33.2, U5.8 (START_SYNC)

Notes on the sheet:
Differential filter (between inputs) should be set 1/10th - 1/100th of ADC f_MOD (while being 10x digital filter) and common mode caps should be 1/10 of the differential. Use NP0 where possible, X7R otherwise.
Load Cells
LC_B_EX-
LC_C_EX-
To MCU ADC as it good enough™ for this
MIPA Pres Sensors
Therefore filter should be 7180<f<25600 Hz. Choose cutoff frequency 10kHz.
LC_A_EX+
LC_B_EX+
Filters have a -3dB point at 10.2kHz
LC_C_EX+
LC_A_EX-
Filters have a -3dB point at 800 Hz and voltage dividers 5V->3.31V
For thermocouples will connect to a XE-1107-001 fascia pannel externally
Will bias by connecing internal VBIAS to negative lead. Elliminates current loss from resistor biasing. https://www.ti.com/lit/an/sbaa274a/sbaa274a.pdf

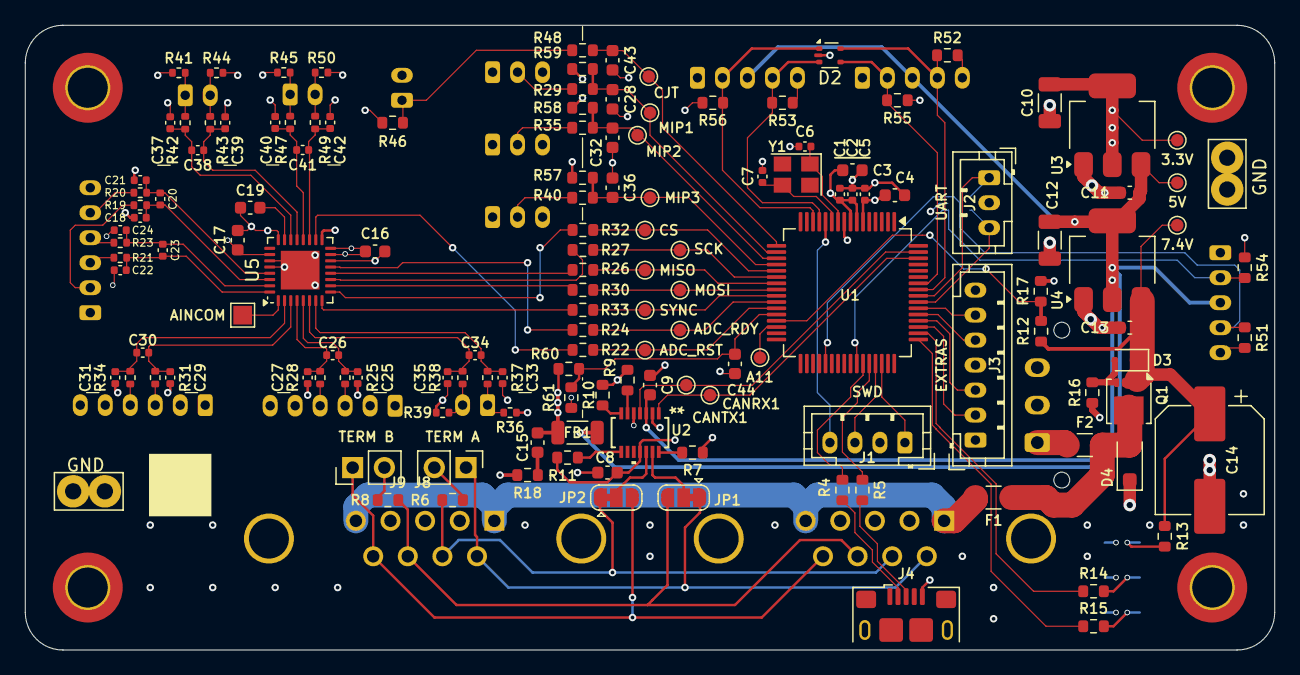
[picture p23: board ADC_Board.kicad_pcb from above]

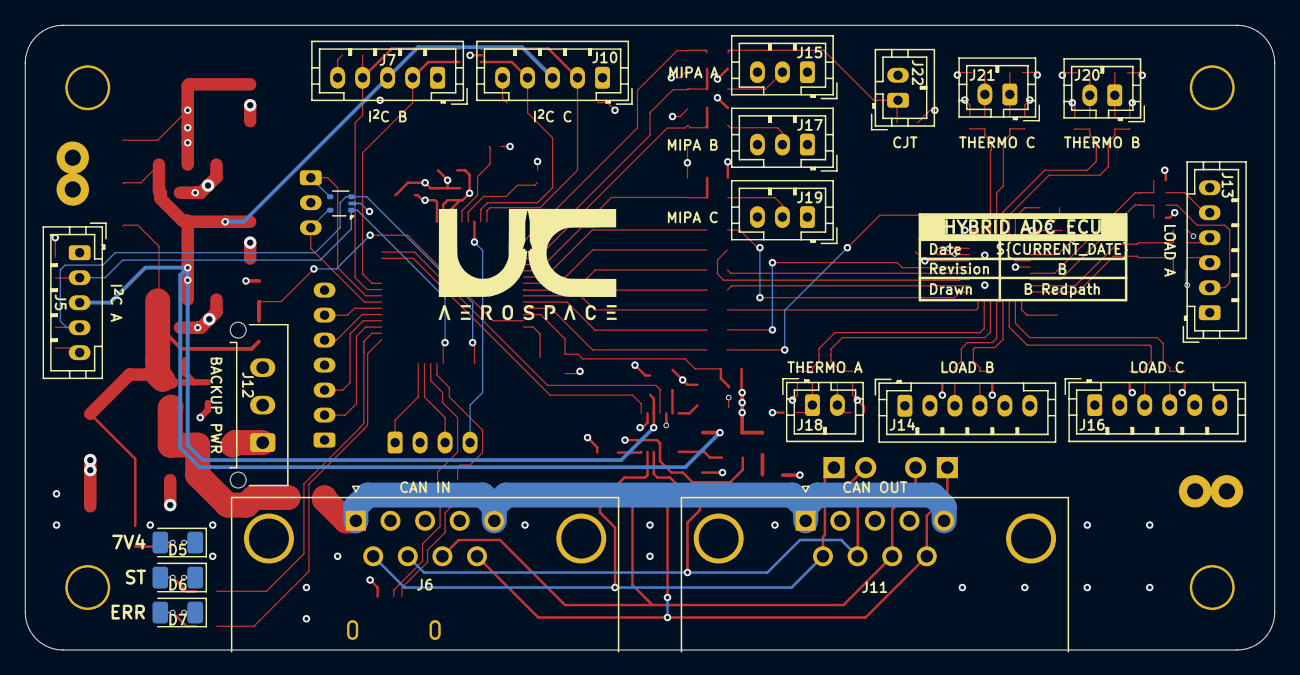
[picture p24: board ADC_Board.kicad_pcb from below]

Board: 4 copper layers, 100.0 x 50.0 mm, 167 parts (20 on the bottom side), 105 nets.

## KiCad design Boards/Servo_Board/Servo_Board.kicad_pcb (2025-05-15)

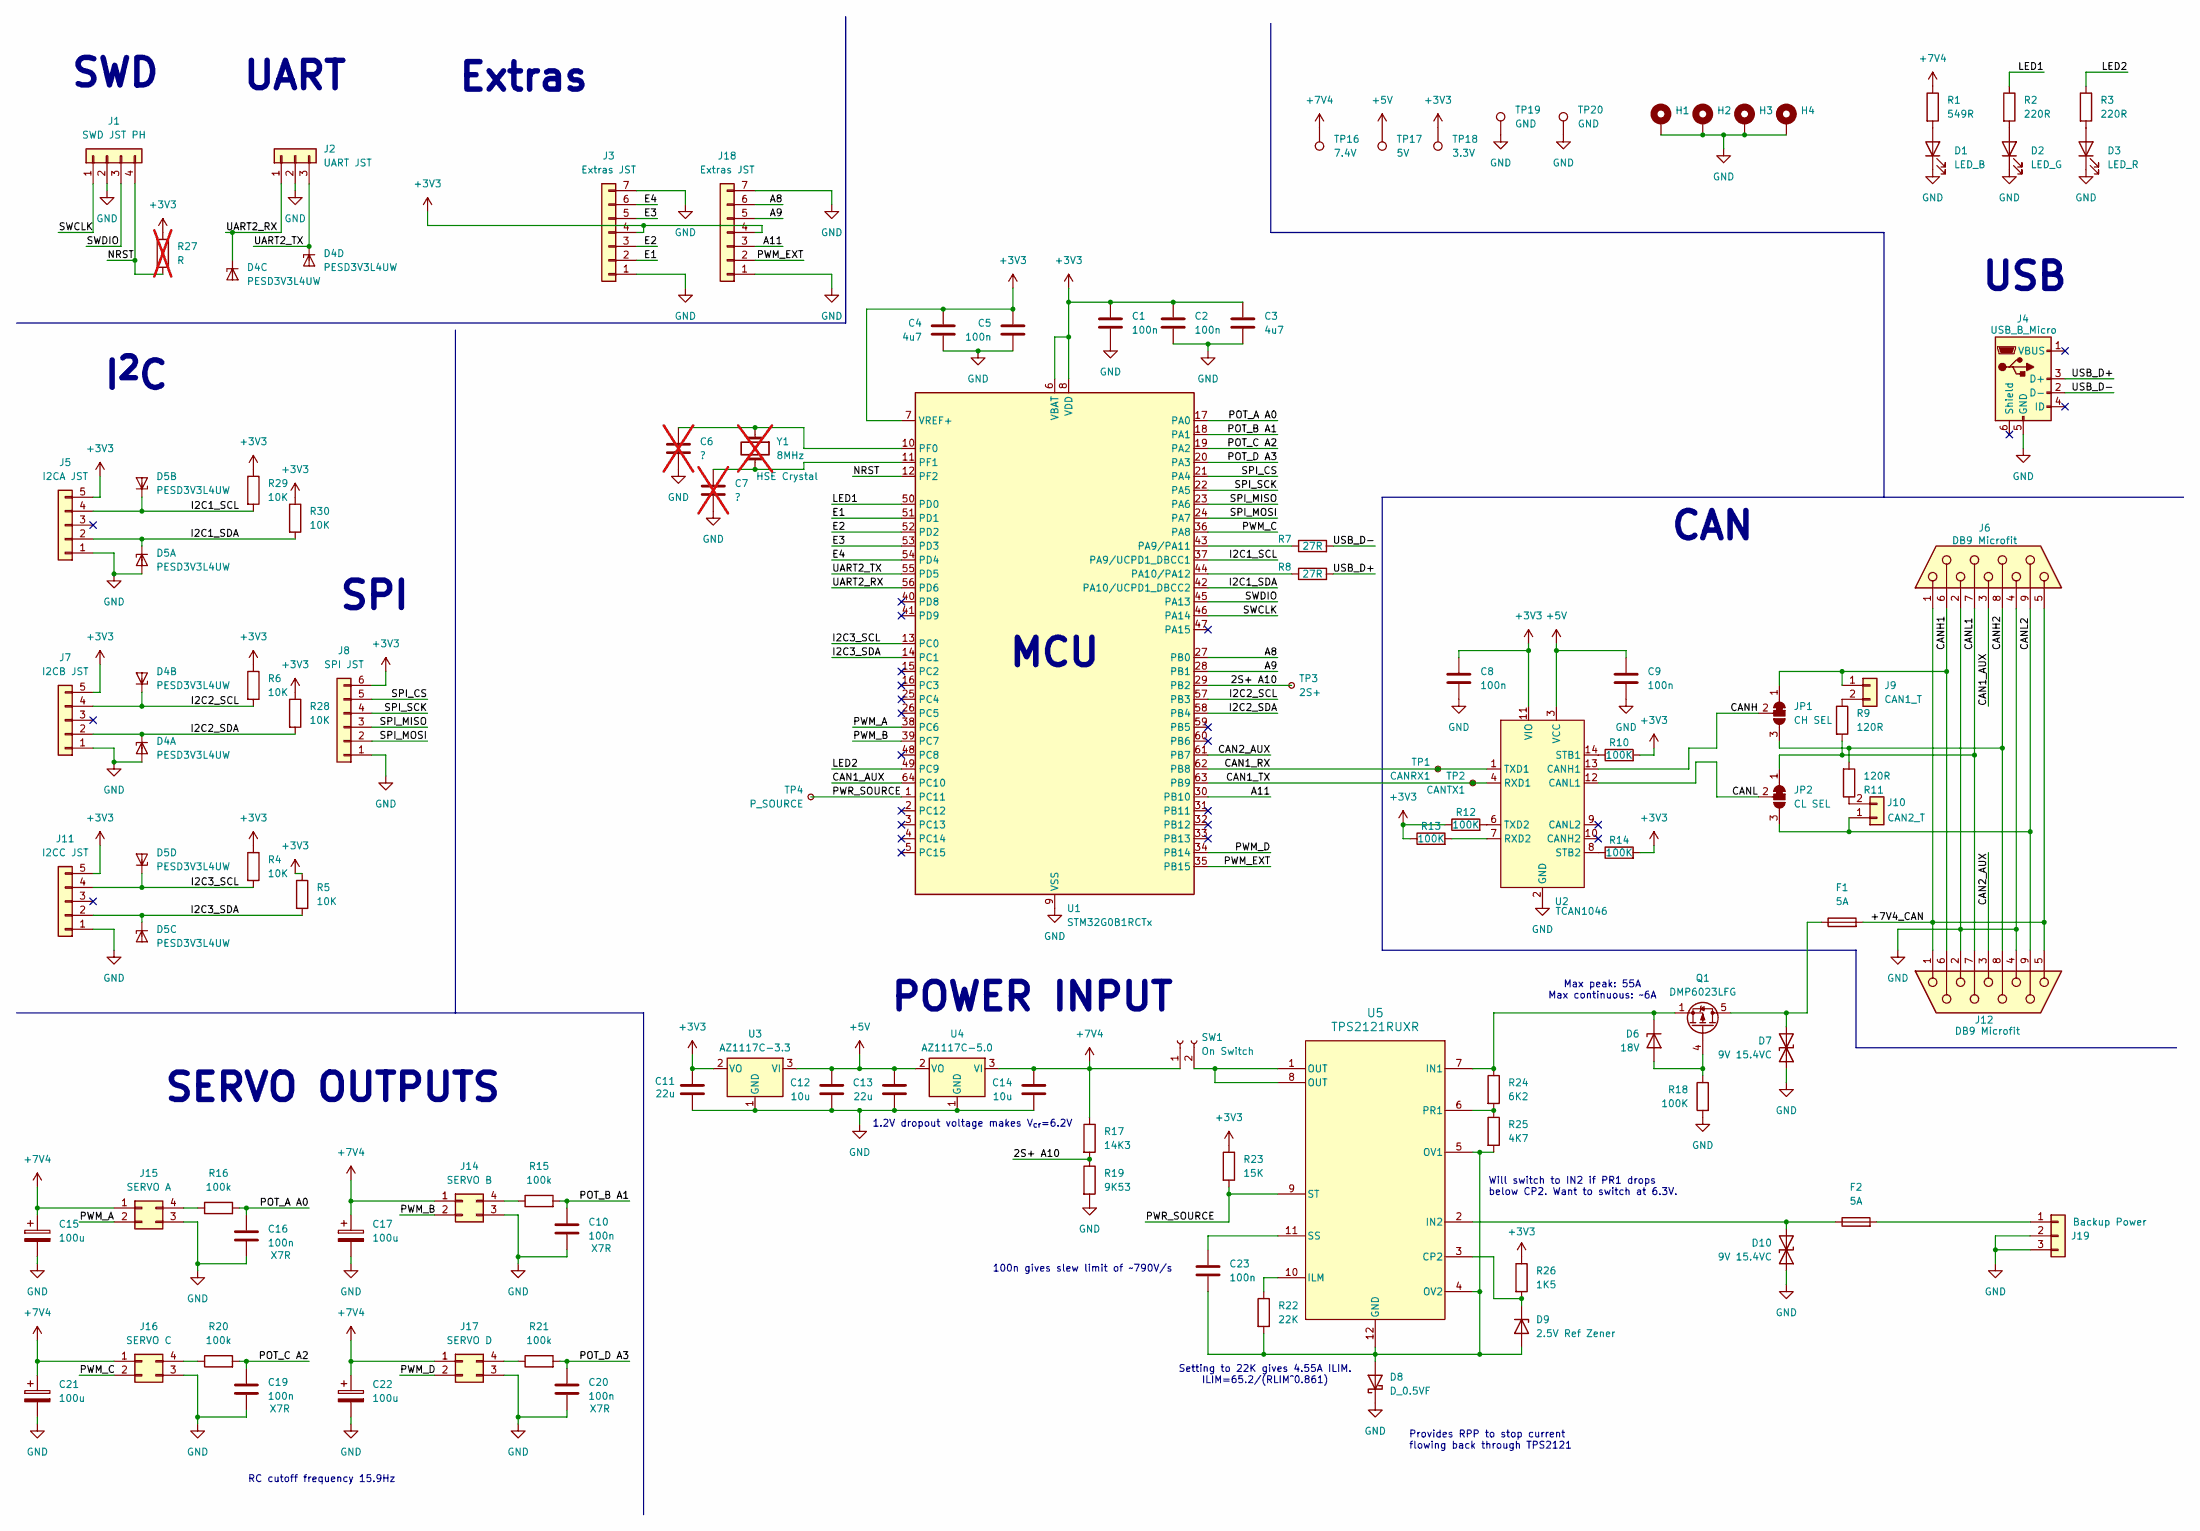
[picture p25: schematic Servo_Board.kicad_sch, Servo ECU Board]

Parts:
C1, C2, C5: 100n; C_0402_1005Metric
C3, C4: 4u7; C_0603_1608Metric
C6, C7: ?; C_0402_1005Metric; not fitted
C8, C9, C10, C16, C19, C20, C23: 100n; C_0603_1608Metric
C11, C13: 22u; C_1206_3216Metric
C12, C14: 10u; C_0603_1608Metric
C15, C17, C21, C22: 100u; CP_Elec_6.3x5.9; MPN SVZ1CM101E06E00RAXXX
D1: LED_B; LED_1206_3216Metric; MPN LTST-C150KRKT
D2: LED_G; LED_1206_3216Metric; MPN LTST-C150KGKT
D3: LED_R; LED_1206_3216Metric; MPN LTST-C150TBKT
D4, D5: PESD3V3L4UW; SOT-665
D6: 18V; D_SOD-323F; MPN MM3Z18VB
D7, D10: 9V 15.4VC; D_SOD-123F; MPN SMF9.0CA
D8: D_0.5VF; D_SOD-523; MPN RB521S30T5G
D9: 2.5V Ref Zener; SOT-23-3; MPN LM4040CYM3-2.5-TR
F1, F2: 5A; Fuse_1206_3216Metric
H1, H2, H3, H4: MountingHole_3.2mm_M3_DIN965_Pad_TopOnly
J1: SWD JST PH; JST_PH_B4B-PH-K_1x04_P2.00mm_Vertical; MPN B4B-PH-K-S
J2: UART JST; JST_PH_B3B-PH-K_1x03_P2.00mm_Vertical; MPN B3B-PH-K-S
J3, J18: Extras JST; JST_PH_B7B-PH-K_1x07_P2.00mm_Vertical; MPN B7B-PH-K-S
J4: USB_B_Micro; USB_Micro-B_Amphenol_10118193-0001LF_Horizontal; MPN 10118193-0001LF
J5: I2CA JST; JST_PH_B5B-PH-K_1x05_P2.00mm_Vertical; MPN B6B-PH-K-S
J6, J12: DB9 Microfit; DSUB-9_Pins_Horizontal_P2.77x2.84mm_EdgePinOffset7.70mm_Hou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; MPN 0430451027
J7: I2CB JST; JST_PH_B5B-PH-K_1x05_P2.00mm_Vertical; MPN B5B-PH-K-S
J8: SPI JST; JST_PH_B6B-PH-K_1x06_P2.00mm_Vertical
J9: CAN1_T; PinHeader_1x02_P2.54mm_Vertical
J10: CAN2_T; PinHeader_1x02_P2.54mm_Vertical
J11: I2CC JST; JST_PH_B5B-PH-K_1x05_P2.00mm_Vertical; MPN B5B-PH-K-S
J14: SERVO B; Molex_Micro-Fit_3.0_43045-0412_2x02_P3.00mm_Vertical; MPN 0430450412
J15: SERVO A; Molex_Micro-Fit_3.0_43045-0412_2x02_P3.00mm_Vertical; MPN 0430450412
J16: SERVO C; Molex_Micro-Fit_3.0_43045-0412_2x02_P3.00mm_Vertical; MPN 0430450412
J17: SERVO D; Molex_Micro-Fit_3.0_43045-0412_2x02_P3.00mm_Vertical; MPN 0430450412
J19: Backup Power; Molex_Micro-Fit_3.0_43650-0315_1x03_P3.00mm_Vertical; MPN 436500315
JP1: CH SEL; SolderJumper-3_P1.3mm_Bridged12_RoundedPad1.0x1.5mm
JP2: CL SEL; SolderJumper-3_P1.3mm_Bridged12_RoundedPad1.0x1.5mm
Q1: DMP6023LFG; Diodes_PowerDI3333-8; MPN DMP6023LFG-7
R1: 549R; R_0603_1608Metric
R2, R3: 220R; R_0603_1608Metric
R4, R5, R6, R28, R29, R30: 10K; R_0603_1608Metric
R7, R8: 27R; R_0603_1608Metric
R9, R11: 120R; R_0603_1608Metric
R10, R12, R13, R14, R18: 100K; R_0603_1608Metric
R15, R16, R20, R21: 100k; R_0603_1608Metric
R17: 14K3; R_0603_1608Metric
R19: 9K53; R_0603_1608Metric
R22: 22K; R_0603_1608Metric
R23: 15K; R_0603_1608Metric
R24: 6K2; R_0603_1608Metric
R25: 4K7; R_0603_1608Metric
R26: 1K5; R_0603_1608Metric
R27: R; R_0603_1608Metric; not fitted
SW1: On Switch; Molex_Micro-Fit_3.0_43650-0215_1x02_P3.00mm_Vertical; MPN 436500228
TP1: CANRX1; TestPoint_Pad_D1.0mm
TP2: CANTX1; TestPoint_Pad_D1.0mm
TP3: 2S+; TestPoint_Pad_D1.0mm
TP4: P_SOURCE; TestPoint_Pad_D1.0mm
TP16: 7.4V; TestPoint_Pad_D1.0mm
TP17: 5V; TestPoint_Pad_D1.0mm
TP18: 3.3V; TestPoint_Pad_D1.0mm
TP19, TP20: GND; TestPoint_Bridge_Pitch2.54mm_Drill1.3mm
U1: STM32G0B1RCTx; LQFP-64_10x10mm_P0.5mm; MPN STM32G0B1RCT6
U2: TCAN1046; SOT23_DYY_TEX; MPN TCAN1046AVDYYRQ1
U3: AZ1117C-3.3; SOT-223-3_TabPin2; MPN AZ1117CH-3.3TRG1
U4: AZ1117C-5.0; SOT-223-3_TabPin2; MPN AZ1117CH-5.0TRG1
U5: TPS2121RUXR; RUX0012A; MPN TPS2121RUXR
Y1: 8MHz; Crystal_SMD_Abracon_ABM8G-4Pin_3.2x2.5mm; not fitted

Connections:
+3V3: C1.1, C2.1, C3.1, C4.1, C5.1, C8.1, C11.1, J3.4, J5.5, J7.5, J8.6, J11.5, J18.4, R4.1, R5.1, R6.1, R10.2, R12.1, R13.1, R14.2, R23.1, R26.1, R27.2, R28.1, R29.1, R30.1, TP18.1, U1.6 (VBAT), U1.7 (VREF+), U1.8 (VDD), U2.11 (VIO), U3.2 (VO)
+5V: C9.1, C12.1, C13.1, TP17.1, U2.3 (VCC), U3.3 (VI), U4.2 (VO)
+7V4: C14.1, C15.1, C17.1, C21.1, C22.1, J14.1, J15.1, J16.1, J17.1, R1.1, R17.1, SW1.1, TP16.1, U4.3 (VI)
/2S+ A10: R17.2, R19.1, TP3.1, U1.29 (PB2)
/+7V4_CAN: F1.2, J6.1, J6.5, J12.1, J12.5
/A8: J18.6, U1.27 (PB0)
/A9: J18.5, U1.28 (PB1)
/A11: J18.3, U1.30 (PB10)
/CAN1_AUX: J6.3, U1.64 (PC10)
/CAN1_RX: TP1.1, U1.62 (PB8), U2.1 (TXD1)
/CAN1_TX: TP2.1, U1.63 (PB9), U2.4 (RXD1)
/CAN2_AUX: J12.3, U1.61 (PB7)
/CANH: JP1.2 (C), U2.13 (CANH1)
/CANH1: J6.6, J9.1, J12.6, JP1.1 (A)
/CANH2: J6.8, J12.8, JP1.3 (B), R11.2
/CANL: JP2.2 (C), U2.12 (CANL1)
/CANL1: J6.7, J12.7, JP2.1 (A), R9.2
/CANL2: J6.9, J10.1, J12.9, JP2.3 (B)
/E1: J3.2, U1.51 (PD1)
/E2: J3.3, U1.52 (PD2)
/E3: J3.5, U1.53 (PD3)
/E4: J3.6, U1.54 (PD4)
/I2C1_SCL: D5.3 (K2), J5.4, R29.2, U1.37 (PA9/UCPD1_DBCC1)
/I2C1_SDA: D5.1 (K1), J5.2, R30.2, U1.42 (PA10/UCPD1_DBCC2)
/I2C2_SCL: D4.3 (K2), J7.4, R6.2, U1.57 (PB3)
/I2C2_SDA: D4.1 (K1), J7.2, R28.2, U1.58 (PB4)
/I2C3_SCL: D5.5 (K4), J11.4, R4.2, U1.13 (PC0)
/I2C3_SDA: D5.4 (K3), J11.2, R5.2, U1.14 (PC1)
/LED1: R2.1, U1.50 (PD0)
/LED2: R3.1, U1.49 (PC9)
/NRST: J1.4, R27.1, U1.12 (PF2)
/POT_A A0: C16.1, R16.2, U1.17 (PA0)
/POT_B A1: C10.1, R15.2, U1.18 (PA1)
/POT_C A2: C19.1, R20.2, U1.19 (PA2)
/POT_D A3: C20.1, R21.2, U1.20 (PA3)
/PWM_A: J15.2, U1.38 (PC6)
/PWM_B: J14.2, U1.39 (PC7)
/PWM_C: J16.2, U1.36 (PA8)
/PWM_D: J17.2, U1.34 (PB14)
/PWM_EXT: J18.2, U1.35 (PB15)
/PWR_SOURCE: R23.2, TP4.1, U1.1 (PC11), U5.9 (ST)
/SPI_CS: J8.5, U1.21 (PA4)
/SPI_MISO: J8.3, U1.23 (PA6)
/SPI_MOSI: J8.2, U1.24 (PA7)
/SPI_SCK: J8.4, U1.22 (PA5)
/SWCLK: J1.1, U1.46 (PA14)
/SWDIO: J1.3, U1.45 (PA13)
/UART2_RX: D4.4 (K3), J2.1, U1.56 (PD6)
/UART2_TX: D4.5 (K4), J2.3, U1.55 (PD5)
/USB_D+: J4.3 (D+), R8.2
/USB_D-: J4.2 (D-), R7.2
GND: C1.2, C2.2, C3.2, C4.2, C5.2, C6.2, C7.2, C8.2, C9.2, C10.2, C11.2, C12.2, C13.2, C14.2, C15.2, C16.2, C17.2, C19.2, C20.2, C21.2, C22.2, D1.1 (K), D2.1 (K), D3.1 (K), D4.2 (A), D5.2 (A), D7.1 (A1), D8.1 (K), D10.1 (A1), H1.1, H2.1, H3.1, H4.1, J1.2, J2.2, J3.1, J3.7, J4.5 (GND), J5.1, J6.2, J6.4, J7.1, J8.1, J11.1, J12.2, J12.4, J14.3, J15.3, J16.3, J17.3, J18.1, J18.7, J19.2, J19.3, R18.2, R19.2, TP19.1, TP20.1, U1.9 (VSS), U2.2 (GND), U2.5 (GND), U3.1 (GND), U4.1 (GND)
unnamed: D1.2 (A), R1.2
unnamed: D2.2 (A), R2.2
unnamed: D3.2 (A), R3.2
unnamed: D6.2 (A), Q1.4 (G), R18.1
unnamed: D6.1 (K), Q1.1 (S), Q1.2 (S), Q1.3 (S), R24.1, U5.7 (IN1)
unnamed: D7.2 (A2), F1.1, Q1.5 (D)
unnamed: C23.2, D8.2 (A), D9.2 (A), R22.2, R25.2, U5.4 (OV2), U5.5 (OV1), U5.12 (GND)
unnamed: D9.1 (K), R26.2, U5.3 (CP2)
unnamed: D10.2 (A2), F2.1, U5.2 (IN2)
unnamed: J9.2, R9.1
unnamed: J10.2, R11.1
unnamed: J14.4, R15.1
unnamed: J15.4, R16.1
unnamed: J16.4, R20.1
unnamed: J17.4, R21.1
unnamed: F2.2, J19.1
unnamed: SW1.2, U5.1 (OUT), U5.8 (OUT)
unnamed: R7.1, U1.43 (PA9/PA11)
unnamed: R8.1, U1.44 (PA10/PA12)
unnamed: C6.1, U1.10 (PF0), Y1.1
unnamed: C7.1, U1.11 (PF1), Y1.3 (2)
unnamed: R13.2, U2.7 (RXD2)
unnamed: R10.1, U2.14 (STB1)
unnamed: R14.1, U2.8 (STB2)
unnamed: R12.2, U2.6 (TXD2)
unnamed: R22.1, U5.10 (ILM)
unnamed: R24.2, R25.1, U5.6 (PR1)
unnamed: C23.1, U5.11 (SS)

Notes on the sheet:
Extras
Max peak: 55A Max continuous: ~6A
SPI
MCU
CAN
Will switch to IN2 if PR1 drops below CP2. Want to switch at 6.3V.
RC cutoff frequency 15.9Hz
POWER INPUT
UART
I^{2}C
SERVO OUTPUTS
100n gives slew limit of ~790V/s
Setting to 22K gives 4.55A ILIM. ILIM=65.2/(RLIM^0.861)
1.2V dropout voltage makes V_{cr}=6.2V
USB
Provides RPP to stop current flowing back through TPS2121
SWD

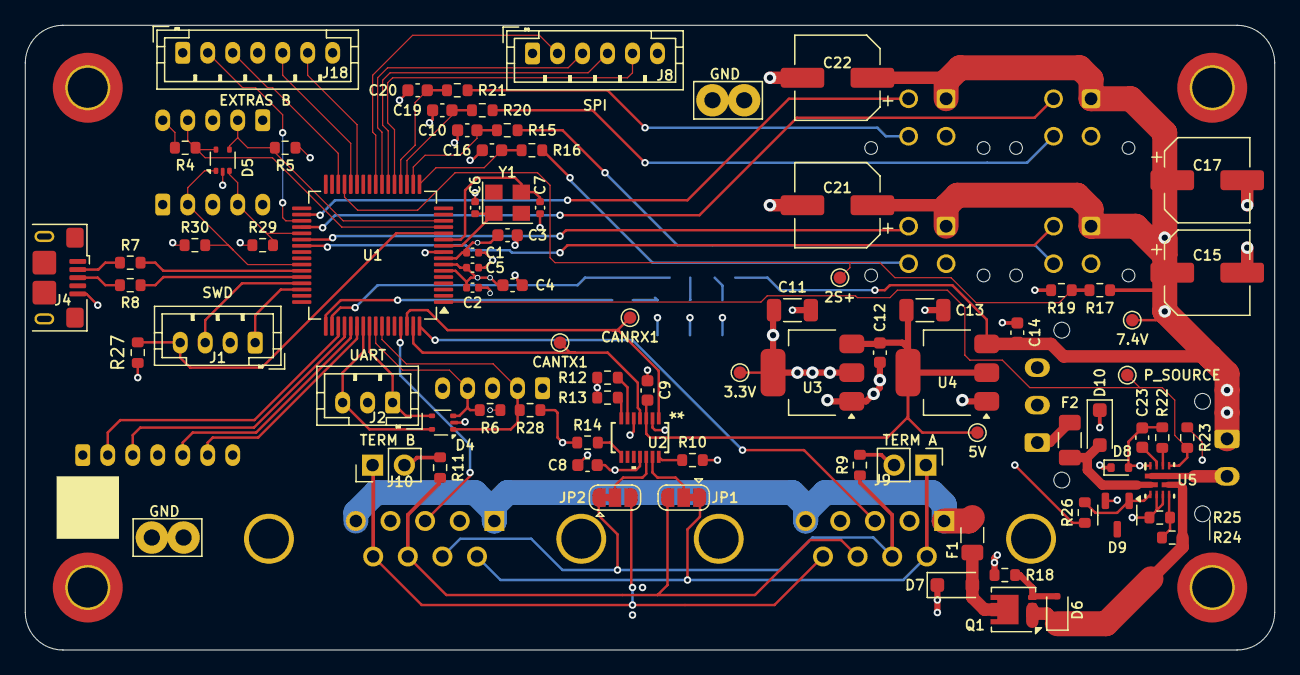
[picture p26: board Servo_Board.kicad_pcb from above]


Board: 4 copper layers, 100.0 x 50.0 mm, 105 parts (18 on the bottom side), 80 nets.

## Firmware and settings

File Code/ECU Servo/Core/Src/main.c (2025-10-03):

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
/* Includes ------------------------------------------------------------------*/
#include "main.h"
#include "usb_device.h"

/* USER CODE BEGIN Includes */
#include "app.h"
/* USER CODE END Includes */

ADC_HandleTypeDef hadc1;
DMA_HandleTypeDef hdma_adc1;

FDCAN_HandleTypeDef hfdcan1;

I2C_HandleTypeDef hi2c1;
I2C_HandleTypeDef hi2c2;
I2C_HandleTypeDef hi2c3;

RTC_HandleTypeDef hrtc;

SPI_HandleTypeDef hspi1;

TIM_HandleTypeDef htim1;
TIM_HandleTypeDef htim2;
TIM_HandleTypeDef htim3;
TIM_HandleTypeDef htim14;
TIM_HandleTypeDef htim15;

UART_HandleTypeDef huart2;

void SystemClock_Config(void);
static void MX_GPIO_Init(void);
static void MX_DMA_Init(void);
static void MX_FDCAN1_Init(void);
static void MX_I2C1_Init(void);
static void MX_I2C2_Init(void);
static void MX_SPI1_Init(void);
static void MX_USART2_UART_Init(void);
static void MX_ADC1_Init(void);
static void MX_RTC_Init(void);
static void MX_TIM1_Init(void);
static void MX_TIM3_Init(void);
static void MX_TIM15_Init(void);
static void MX_I2C3_Init(void);
static void MX_TIM14_Init(void);
static void MX_TIM2_Init(void);
/**
  * @brief  The application entry point.
  * @retval int
  */
int main(void)
{

  /* MCU Configuration--------------------------------------------------------*/

  /* Reset of all peripherals, Initializes the Flash interface and the Systick. */
  HAL_Init();

  /* Configure the system clock */
  SystemClock_Config();

  /* USER CODE BEGIN SysInit */

  /*****************
   * Start TIM2 for timebase
   *****************/

  MX_TIM2_Init();

  // Set counter to zero
  __HAL_TIM_SET_COUNTER(&htim2, 0);
  
  // Start the timer
  if (HAL_TIM_Base_Start(&htim2) != HAL_OK) {
      Error_Handler();
  }

  /* USER CODE END SysInit */

  /* Initialize all configured peripherals */
  MX_GPIO_Init();
  MX_DMA_Init();
  MX_FDCAN1_Init();
  MX_I2C1_Init();
  MX_I2C2_Init();
  MX_SPI1_Init();
  MX_USART2_UART_Init();
  MX_ADC1_Init();
  MX_RTC_Init();
  MX_TIM1_Init();
  MX_TIM3_Init();
  MX_TIM15_Init();
  MX_I2C3_Init();
  //MX_USB_Device_Init();
  MX_TIM14_Init();
  MX_TIM2_Init();
  /* USER CODE BEGIN 2 */
  app_init(); // Initialize the application
  app_run(); // Run the application
  /* USER CODE END 2 */

  /* Infinite loop */
  /* USER CODE BEGIN WHILE */
  while (1)
  {
    /* USER CODE END WHILE */

    /* USER CODE BEGIN 3 */
  }
  /* USER CODE END 3 */
}

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


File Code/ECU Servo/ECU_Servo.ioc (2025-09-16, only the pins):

Mcu.UserName=STM32G0B1RCTx
PA0.GPIO_Label=POT_A
PA0.Signal=ADC1_IN0
PA1.GPIO_Label=POT_B
PA1.Signal=ADC1_IN1
PA10.Signal=I2C1_SDA
PA13.Signal=SYS_SWDIO
PA14-BOOT0.Signal=SYS_SWCLK
PA2.GPIO_Label=POT_C
PA2.Signal=ADC1_IN2
PA3.GPIO_Label=POT_D
PA3.Signal=ADC1_IN3
PA4.Signal=SPI1_NSS
PA5.Signal=SPI1_SCK
PA6.Signal=SPI1_MISO
PA7.Signal=SPI1_MOSI
PA8.GPIO_Label=PWM_C
PA8.Signal=S_TIM1_CH1
PA9.Signal=I2C1_SCL
PB14.GPIO_Label=PWM_D
PB14.Signal=S_TIM15_CH1
PB2.GPIO_Label=ADC_2S
PB2.Signal=ADC1_IN10
PB3.Signal=I2C2_SCL
PB4.Signal=I2C2_SDA
PB7.GPIO_Label=CAN2_AUX
PB7.Signal=GPIO_Input
PB8.Signal=FDCAN1_RX
PB9.Signal=FDCAN1_TX
PC0.Signal=I2C3_SCL
PC1.Signal=I2C3_SDA
PC10.GPIO_Label=CAN1_AUX
PC10.Signal=GPIO_Input
PC11.GPIO_Label=PWR_SOURCE
PC11.Signal=GPIO_Input
PC6.GPIO_Label=PWM_A
PC6.Signal=S_TIM3_CH1
PC7.GPIO_Label=PWM_B
PC7.Signal=S_TIM3_CH2
PC9.GPIO_Label=LED_ERROR
PC9.Signal=GPIO_Output
PD0.GPIO_Label=LED_STATUS
PD0.Signal=GPIO_Output
PD1.GPIO_Label=Servo_A_NRST
PD1.Signal=GPIO_Output
PD2.GPIO_Label=Servo_B_NRST
PD2.Signal=GPIO_Output
PD3.GPIO_Label=Servo_C_NRST
PD3.Signal=GPIO_Output
PD4.GPIO_Label=Servo_D_NRST
PD4.Signal=GPIO_Output
PD5.Signal=USART2_TX
PD6.Signal=USART2_RX

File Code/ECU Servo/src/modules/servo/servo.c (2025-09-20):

#include "servo.h"
#include "adc.h"
#include "debug_io.h"
#include "can.h"
#include "fsm.h"
#include "error_def.h"

static ServoQueue servoQueue = {
    .items = {0},
    .head = 0,
    .tail = 0
};

static uint16_t servoPositions[4];

/************
 * Private functions
 ************/

// Sets the position of the servo as a fraction of 1000 steps (0 to 1000)
static void servo_set_angle(Servo *servo, uint16_t angle);
// Internal helper: remove all queued items for a servo
static void servo_queue_remove_for_servo(Servo *servo);
// Internal helper: queue a position for a servo
static void servo_queue_position(Servo *servo, uint16_t position);

/************
 * Servo instances
 ************/

// Servo Channel 1
Servo servoVent = {
    .tim = &htim3,
    .channel = TIM_CHANNEL_1,
    .state = SERVO_STATE_DISARMED,
    .closePosition = 500,
    .openPosition = 150,
    .targetPosition = 500,
    .currentPosition = 0,
    .nrstPin = GPIO_PIN_1, // NRST pin for servo 1
    .nrstPort = GPIOD // NRST port for servo 1
};

// Servo Channel 2
Servo servoNitrogen = {
    .tim = &htim3,
    .channel = TIM_CHANNEL_2,
    .state = SERVO_STATE_DISARMED,
    .closePosition = 450,
    .openPosition = 0,
    .targetPosition = 450,
    .currentPosition = 0,
    .nrstPin = GPIO_PIN_2, // NRST pin for servo 2
    .nrstPort = GPIOD // NRST port for servo 2
};

// Servo Channel 3
Servo servoNitrousA = {
    .tim = &htim1,
    .channel = TIM_CHANNEL_1,
    .state = SERVO_STATE_DISARMED,
    .closePosition = 550,
    .openPosition = 50,
    .targetPosition = 550,
    .currentPosition = 0,
    .nrstPin = GPIO_PIN_3, // NRST pin for servo 3
    .nrstPort = GPIOD // NRST port for servo 3
};

// Servo Channel 4
Servo servoNitrousB = {
    .tim = &htim15,
    .channel = TIM_CHANNEL_1,
    .state = SERVO_STATE_DISARMED,
    .closePosition = 700,
    .openPosition = 200,
    .targetPosition = 700,
    .currentPosition = 0,
    .nrstPin = GPIO_PIN_4, // NRST pin for servo 4
    .nrstPort = GPIOD // NRST port for servo 4
};

Servo* servoByIndex[4] = {
    &servoVent,
    &servoNitrogen,
    &servoNitrousA,
    &servoNitrousB
};

/************
 * Public functions
 ************/

void servo_init(void) {
    servo_update_positions(); // Initialize servo positions from ADC
    servo_queue_clear();
}

void servo_send_status(void) {
    uint8_t fsm_status = (uint8_t)fsm_get_state();
    uint8_t servo_status = 0;
    for (int i = 3; i >= 0; i--) {
        servo_status |= (servoByIndex[i]->state & 0x03) << (i * 2);
    }
    can_send_status(CAN_NODE_TYPE_CENTRAL, CAN_NODE_ADDR_CENTRAL, fsm_status, servo_status);
}

void servo_send_can_positions(void) 
{
    servo_update_positions();

    uint8_t setPos[4] = {0};
    for (int i = 0; i < 4; i++) {
        uint8_t setposition;
        bool setIsOpen = (servoByIndex[i]->targetPosition == servoByIndex[i]->openPosition);
        bool setIsClose = (servoByIndex[i]->targetPosition == servoByIndex[i]->closePosition);
        if (setIsOpen) {
            setposition = 1; // Open position
        } else if (setIsClose) {
            setposition = 0; // Close position
        } else {
            setposition = 2; // Crack position (not implemented, default to 0)
        }
        setPos[i] = (setposition << 6) | (servoByIndex[i]->targetPosition / 50);
    }
    uint8_t currentPos[4] = {0};
    for (int i = 0; i < 4; i++) {
        bool atPosition = false;
        int16_t delta = (int16_t)servoByIndex[i]->targetPosition - servoByIndex[i]->currentPosition;
        if (delta < 0) delta = -delta;
        if (delta <= SERVO_POSITION_TOLERANCE*3) {
            atPosition = true;
        }
        currentPos[i] = (servoByIndex[i]->state << 6) | (atPosition << 5) | (servoByIndex[i]->currentPosition / 50);
    }
    can_send_servo_position(CAN_NODE_TYPE_CENTRAL, CAN_NODE_ADDR_CENTRAL, 0b1111, setPos, currentPos); // Assume all are connected
}

void servo_arm(Servo *servo) 
{
    // Enable the servo
    servo->state = SERVO_STATE_ARMED;
    servo_send_status();
    HAL_GPIO_WritePin(servo->nrstPort, servo->nrstPin, GPIO_PIN_SET); // Set NRST pin high to enable servo
}

void servo_disarm(Servo *servo) {
    // Disable the servo and stop PWM
    servo->state = SERVO_STATE_DISARMED;
    servo_send_status();
    HAL_TIM_PWM_Stop(servo->tim, servo->channel);
    HAL_GPIO_WritePin(servo->nrstPort, servo->nrstPin, GPIO_PIN_RESET); // Set NRST pin low to reset servo
    // Return to safe target and clear any queued moves for this servo
    // servo->targetPosition = servo->safePosition; // 
    servo_queue_remove_for_servo(servo);
}

void servo_disarm_all(void) {
    for (uint8_t i = 0; i < 4; i++) {
        servo_disarm(servoByIndex[i]);
    }
}

// Sets the position of the servo, will queue if armed or moving
// This can be done externally
void servo_set_position(Servo *servo, uint16_t position) {
    if (servo->state == SERVO_STATE_ERROR) {
        dbg_printf("Error: Servo is in error state, cannot set position.\r\n");
        return;
    }

    // Set the target position
    servo->targetPosition = position;
    if (servo->state == SERVO_STATE_ARMED || servo->state == SERVO_STATE_MOVING) {
        servo_queue_position(servo, position);
    }
}

// Poll the servo queue for the next item to process. Done from FSM
bool servo_queue_poll() 
{
    // Process the servo queue
    if (servoQueue.head != servoQueue.tail) {
        ServoQueueItem item = servoQueue.items[servoQueue.head];

        // Set the servo position
        servo_set_angle(item.servo, item.position);
        // Set state to moving and start the PWM
        item.servo->state = SERVO_STATE_MOVING; 
        HAL_TIM_PWM_Start(item.servo->tim, item.servo->channel);
        servo_send_status();

        return true; // Successfully processed an item
    }
    return false; // No items to process
}

// Done in move mode in the FSM to check if current move completed.
bool servo_queue_check_complete()
{
    if (servoQueue.head != servoQueue.tail) {
        servo_update_positions(); // Update current positions from ADC
        ServoQueueItem *item = &servoQueue.items[servoQueue.head];
        int16_t delta = (int16_t)item->position - item->servo->currentPosition;
        if (delta < 0) delta = -delta;
        if (delta <= SERVO_POSITION_TOLERANCE) {
            return true; // Item is complete
        }
    }
    return false; // No complete items
}
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

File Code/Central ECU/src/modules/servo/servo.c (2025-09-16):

#include "servo.h"
#include "can.h"
#include "debug_io.h"

static servo_feedback_t states[4];
static servo_status_u servo_status;

void servo_update(servo_feedback_t feedback[4])
{
    for(int i=0; i<4; i++){
        states[i] = feedback[i];
    }
}

void servo_get_states(servo_feedback_t feedback[4])
{
    for(int i=0; i<4; i++){
        feedback[i] = states[i];
    }
}

void servo_set_position(uint8_t servo_id, servo_positions_t position)
{
    if(servo_id > 3) {
        dbg_printf("SERVO: ERROR, invalid servo ID %d\n", servo_id);
        return;
    }
    dbg_printf("SERVO: Set servo %d to position %d\n", servo_id, position);
    can_send_command(CAN_NODE_TYPE_SERVO, CAN_NODE_ADDR_BROADCAST, CAN_CMD_SET_SERVO_POS, servo_id << 6 | position);
}

void servo_arm_all(void)
{
    dbg_printf("SERVO: ARM ALL\n");
    can_send_command(CAN_NODE_TYPE_SERVO, CAN_NODE_ADDR_BROADCAST, CAN_CMD_SET_SERVO_ARM, 0xFF);
}

void servo_disarm_all(void)
{
    dbg_printf("SERVO: DISARM ALL\n");
    can_send_command(CAN_NODE_TYPE_SERVO, CAN_NODE_ADDR_BROADCAST, CAN_CMD_SET_SERVO_ARM, 0xF0);
}

void servo_print_current_state(void)
{
    dbg_printf("SERVO: Current States:\n");
    dbg_printf("  ID | SetPos | State   | AtSetPos | CurrPos\n");
    dbg_printf(" ----|--------|---------|----------|--------\n");
    dbg_printf("  %d |   %d    |   %d     |    %d     |   %d\n", 0, states[0].setPos, states[0].state, states[0].atSetPos, states[0].currentPos);
    dbg_printf("  %d |   %d    |   %d     |    %d     |   %d\n", 1, states[1].setPos, states[1].state, states[1].atSetPos, states[1].currentPos);
    dbg_printf("  %d |   %d    |   %d     |    %d     |   %d\n", 2, states[2].setPos, states[2].state, states[2].atSetPos, states[2].currentPos);
    dbg_printf("  %d |   %d    |   %d     |    %d     |   %d\n", 3, states[3].setPos, states[3].state, states[3].atSetPos, states[3].currentPos);
}

bool servo_helper_check_all_closed(void) 
{
    for (int i = 0; i < 4; i++) {
        if (states[i].setPos != SERVO_POSITION_CLOSE || states[i].atSetPos == false) {
            return false;
        }
    }
    return true;
}

void servo_status_update(uint8_t main_state, uint8_t substates)
{
    servo_status.raw = (servo_state_t) (main_state << 8 | substates);
}

void servo_status_get(servo_status_u* status)
{
    *status = servo_status;
}

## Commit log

2025-03-21 Initial Boilerplate
    [ADC_Board.kicad_pcb, ADC_Board.kicad_sch, Central_ECU.kicad_pcb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]
2025-03-21 MCU + CAN
    [Central_ECU.kicad_sch]
2025-03-22 Added 422 and crystal
    [Central_ECU.kicad_sch]
2025-03-23 Power regulation and crystal for MCU added to servo board.
    [Servo_Board.kicad_sch]
2025-03-27 More to the central mcu plus started on ignitors and valve control
    [Central_ECU.kicad_sch, ign+nc_valve.kicad_sch, pyro_ls.kicad_sch]
2025-03-27 CAN transceiver and D-sub connector
    [Servo_Board.kicad_sch]
2025-03-28 Some more minor tweaks
    [Central_ECU.kicad_sch, ign+nc_valve.kicad_sch]
2025-03-30 Servo board changes:
    Replaced buck converter with LDO voltage regulator.
    Found PWM pins on u-controller and connected them to connectors with flyback diodes.
    [Servo_Board.kicad_sch]
2025-03-30 D-sub output connector added to servo board
    [Servo_Board.kicad_sch]
2025-03-31 Added USB and serial programmer to Servo Board. Added servo feedback lines
    [Servo_Board.kicad_sch]
2025-03-31 Forgot termination resistors
    [Servo_Board.kicad_sch]
2025-04-01 Added most connectors and hooking up
    [Central_ECU.kicad_sch, connectors.kicad_sch, ign+nc_valve.kicad_sch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]
2025-04-01 Nearing completion
    [Central_ECU.kicad_sch, connectors.kicad_sch]
2025-04-02 For review
    [Central_ECU.kicad_sch, connectors.kicad_sch, ign+nc_valve.kicad_sch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]
2025-04-02 Finished Servo board and ADC board for review tomorrow
    [ADC_Board.kicad_sch, Servo_Board.kicad_sch]
2025-04-04 Footprints for the servo and ADC board
    [ADC_Board.kicad_sch, Servo_Board.kicad_sch]
2025-04-06 Changed to 0603 passives and added NRST line
    [Central_ECU.kicad_sch, connectors.kicad_sch, ign+nc_valve.kicad_sch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]
2025-04-12 Added environmental P+T sensor
    [Central_ECU.kicad_sch]
2025-04-12 Started layout
    [436500215.stp, Central_ECU.kicad_pcb]
2025-04-13 More progress on layout
    [Central_ECU.kicad_pcb, Central_ECU.kicad_sch, ign+nc_valve.kicad_sch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]
2025-04-13 Finished central ECU for review
    [Central_ECU.kicad_pcb, Central_ECU.kicad_sch, connectors.kicad_sch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]
2025-04-13 Tidy up, will send to Chris
    [Central_ECU.kicad_pcb, Central_ECU.kicad_sch, connectors.kicad_sch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]
2025-04-13 Added PDF of schematic
2025-04-15 Fixed voltage divider and comparator bias
    Re feedback from Chris still need to fix regulator power dissipation. Happy with other points being non-issues at current.
    [Central_ECU.kicad_pcb, connectors.kicad_sch, ign+nc_valve.kicad_sch]
2025-04-17 Central ECU to order
    [0430450412.stp, 0430451027.stp, 436500315.stp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]
2025-04-17 Rendered and updated pdf plot
    [Central_ECU.kicad_pcb, DYY0014A.stp]
2025-05-05 Ongoing changes to satellite boards and test code
    [ADC_Board.kicad_sch, Analog.kicad_sch, Pressure_Board.kicad_pcb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]
2025-05-12 Somewhat done servo+adc boards
    [ADC_Board.kicad_sch, Analog.kicad_sch, Servo_Board.kicad_sch]
2025-05-12 Fixes and footprints
    Just thermocouples todo
    [ADC_Board.kicad_sch, Analog.kicad_sch, Servo_Board.kicad_sch]
2025-05-12 Selected thermocouple connector, added ferrite bead
    [Analog.kicad_sch]
2025-05-12 Added switch to servo board
    [Servo_Board.kicad_sch]
2025-05-13 Servo nearing completion and ADC 50% layed out
    [ADC_Board.kicad_pcb, ADC_Board.kicad_sch, Analog.kicad_sch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]
2025-05-14 Nearing complete layout on both boards
    [ADC_Board.kicad_pcb, ADC_Board.kicad_sch, Analog.kicad_sch]
2025-05-15 Completed with manufacturing files
    [-B_Cu.gbr, -B_Mask.gbr, -B_Paste.gbr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]
2025-06-06 Cleaning out code for firmware
    [ADC+Servo.xlsx, ADC_Board.csv, ADC_Board.kicad_sch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]
2025-06-06 Prep for ADC+Servo
2025-06-06 Some intital print functions and setting up for UID locking
2025-06-10 Updated resistors on ECU, added code to read battery voltages
    [Central_ECU.kicad_pcb, Central_ECU.kicad_sch, connectors.kicad_sch]
2025-06-12 OLED working and displaying battery percentage
2025-06-13 Turns out SD is problematic
    [ECU_Mainboard.ioc, app.c, config.h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]
2025-06-20 RS422 still an issue
    [ECU_Mainboard.ioc, app.c, debug_io.c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]
2025-07-15 Start code for servo, USB not working
    [diff.csv, diff.txt, results.csv]
2025-07-15 Rev B ADC Board
    Change ADC to QFN due to order error
    Adds voltage divider to MIPA ADC lines
    [ADC_Board-B_Cu.gbr, ADC_Board-B_Mask.gbr, ADC_Board-B_Paste.gbr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]
2025-07-19 Added servo boiler code
2025-07-21 Updates to board to refelct rework state
    [Central_ECU.kicad_sch]
2025-07-28 Some PCB changes after ADC assembly
    [Analog.kicad_sch]
2025-07-28 Changes before branching to make servos work
2025-07-29 Working for serial printing to control servo #1 from ECU over serial
2025-07-31 Still not working but closer, does work after with a patch to the HAL
    [ECU_Mainboard.ioc, app.c, main.c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]
2025-08-01 Changes to reflect incorrect schematic labeling
    [Central_ECU.kicad_pcb, Central_ECU.kicad_sch, connectors.kicad_sch]
2025-08-01 Started on CAN handlers, to merge in servo branch
2025-08-03 A bunch of work on servo board CAN comms and FSM
2025-08-06 ADS now works, needs prototypes, and built in functionality just needs CAN_TX.
2025-08-06 Many changes for the ADC board, getting somewhere
2025-08-06 More slop for ADC board, getting close
    [app.c, can_handlers.c, pte7300.c]
2025-08-22 Files and framework started for new implementation of FSM and sequencer
2025-08-25 All FSM machines written and build without errors. Untested so expected to not work. Extra functionality still missing
    [app.c, can_handlers.c, main_FSM.c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]
2025-08-26 Added print statements to all states machines for testing. Fixed legacy function calls in CAN and RS422.
    [can_handlers.c, main_FSM.c, rs422_handler.c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]
2025-08-26 Sequencer V1 written. Goes through all states and actuates everything. Currently does not check anything and is on auto fire.
2025-08-27 Before pressure testing, fixed CAN clashes
    [ECU_Mainboard.ioc, ECU_Servo.ioc, app.c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]
2025-08-28 Calibrated for new nitrogen servo
2025-08-28 Added checks to sequencer minus SD card and pressures. Mostly commented out because trying to get everything working in wind tunnel.
2025-09-16 Fixed servos, add thermocouple cjt correction, tidy on central ECU
    [ECU_Servo.ioc, adc.c, app.c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]
2025-10-09 Slower post fire sequence after reviewing cold flow
2025-10-29 Hardware README and final change to ADC code

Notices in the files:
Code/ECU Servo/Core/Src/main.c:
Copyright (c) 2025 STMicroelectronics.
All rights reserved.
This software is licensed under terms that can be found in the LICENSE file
